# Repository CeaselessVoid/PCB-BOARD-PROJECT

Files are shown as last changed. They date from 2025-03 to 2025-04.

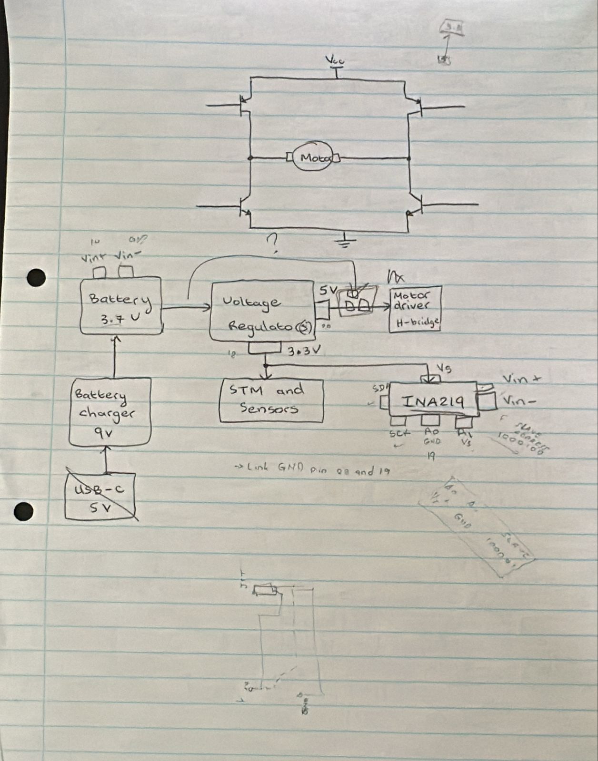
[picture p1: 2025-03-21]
Project_Roadmap.jpeg

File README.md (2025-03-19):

# PCB-BOARD-PROJECT
Currently we still need to flesh out our design in terms of component choice, back up designs and the actual design.
Below is all the data we have currently(the requirements of the project) :
1. Operate up to 4 motors bidirectionally with the pins available to you (listed in the power pinout table). You will need to control 2x brushed DC motors which could each draw 200mA at the highest voltage of a 1S1P battery (the battery is further specified in the battery section).The other 2x motors are for the auxiliary connection and need to operate 500mA each.
2. Place an INA219 for monitoring the battery on the I2C Bus and configure it correctly with respect to the hardware (cannot have BOTH A0 AND A1 on GND)
3. Charge the battery from the 9V input pin (listed in the power pinout table).
4. Have two charging modes for a higher and lower charging current for the battery (200mA, and approximately 600mA ±100mA from the battery perspective.
5. Integrate USB C and get 9V out of the USB Host
6. Provide 2x External Load Switching at 1A each (High Side connected to your 5V)
7. Provide a 3V3 5% accuracy (300mA max) and 5V Out 5% accuracy (1.5A max)
8. Provide an ON/OFF switch. OFF state: battery draw <30uA. ON state: can provide your robot peak current of 2A. The switch needs to shut down 5V and 3V3.

So far we have locked in the components INA219 and possiblely the H-bridge. This will need to be deducted from our budget once we fin a suitable vendor.(As it stands we have $56.5 for the components).
Other points:
1. The board solution should be 82 x 60 (mm)
2. We cannot excede the budget
3. Deadline is the 28th of March (we should try to finalize well before this)
4. All components sourced from JLCPCB

Future things to add here: 
1. We need to add the schemetic and PCB design
2. Possible links to the datasheets we used for an easier time during report writing
3. Any computations we do(again mainly for reference)

https://cdn-shop.adafruit.com/datasheets/ina219.pdf - INA219

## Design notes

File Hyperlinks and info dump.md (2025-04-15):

This section just has links to datasheets and any other valuable info for the project. (Will try my best to keep it neat). It seems the hyperlinks to JLCPCB require a page refresh to show the data. 

1. INA219:
   
i) INA219AIDR:
 - https://jlcpcb.com/api/file/downloadByFileSystemAccessId/8559701789747400704 (Datasheet)
 - [https://jlcpcb.com/parts/componentSearch?searchTxt=INA219 ](https://jlcpcb.com/partdetail/TexasInstruments-INA219AIDR/C138706)(JLCPCB page)
   
ii) INA219AIDCNR: (Chosen)
- https://jlcpcb.com/api/file/downloadByFileSystemAccessId/8586200525100486656 (Linked datasheet but i have my doubts about it)
- [https://jlcpcb.com/parts/componentSearch?searchTxt=INA219](https://jlcpcb.com/partdetail/TexasInstruments-INA219AIDCNR/C87469) (JLCPCB page)
  
The other components in JLCPCB fell into two categories. Either to pricey to consider or too few component count. They ave been ignored.

2. Voltage Regulators:
   
2.1 DC-DC Converter - Boost.

i) HT7750B 
   - https://jlcpcb.com/partdetail/HoltekSemicon-HT7750B/C259932 (JLCPCB page)
   - https://www.alldatasheet.com/datasheet-pdf/view/142973/HOLTEK/HT7750.html (Datasheet)

ii) MT3540-F23 (Chosen)
   - https://jlcpcb.com/partdetail/xi_an_AerosemiTech-MT3540F23/C181783 (JLCPCB page)
   - https://jlcpcb.com/api/file/downloadByFileSystemAccessId/8586200699318751232 (Datasheet)

iii) TPS613222ADBVR
   - https://jlcpcb.com/partdetail/TexasInstruments-TPS613222ADBVR/C2071163 (JLCPCB page)
   - https://www.ti.com/cn/lit/ds/symlink/tps61322.pdf?ts=1742636762086&ref_url=https%253A%252F%252Fjlcpcb.com%252F (Datasheet)

2.2 LDO 

i) HT7533-1
   - https://jlcpcb.com/partdetail/HoltekSemicon-HT75331/C14289 (JLCPCB page)
   - https://jlcpcb.com/api/file/downloadByFileSystemAccessId/8579707787284303872 (Datasheet)
   
ii) AP2112K-3.3TRG1 (Chosen)
   - https://jlcpcb.com/partdetail/DiodesIncorporated-AP2112K_33TRG1/C51118 (JLCPCB page)
   - https://jlcpcb.com/api/file/downloadByFileSystemAccessId/8588881290191360000 (Datasheet)

iii) MIC5219-3.3YM5-TR
   - https://jlcpcb.com/partdetail/MicrochipTech-MIC5219_3_3YM5TR/C29613 (JLCPCB page)
   - https://jlcpcb.com/api/file/downloadByFileSystemAccessId/8586199085112037376 (Datasheet)

iv) TPAP2112K-3.3TRG1
   - https://jlcpcb.com/partdetail/TechPublic-TPAP2112K_33TRG1/C3021085 (JLCPCB page)
   - https://jlcpcb.com/api/file/downloadByFileSystemAccessId/8589835741104021504 (Datasheet)

2.3 Schottky Diodes

i) SS34
- https://jlcpcb.com/partdetail/mdd_microdiode_semiconductor-SS34/C8678 (JLCPCB page)
- https://jlcpcb.com/api/file/downloadByFileSystemAccessId/8586172667489079296 (Datasheet)

2.3 Inductor 

i) FTC252010S4R7MBCA (4.7uH)
   - https://jlcpcb.com/partdetail/6763480-FTC252010S4R7MBCA/C5832360 (JLCPCB page)
   - https://jlcpcb.com/api/file/downloadByFileSystemAccessId/8590904256692510720 (Datasheet)
   
3. Battery Chargers

3.1 TP4056-42-ESOP8
   - https://jlcpcb.com/partdetail/17264-TP4056_42ESOP8/C16581 (JLCPCB page)
   - https://jlcpcb.com/api/file/downloadByFileSystemAccessId/8588879072461508608 (Datasheet)

3.2 MP2617
   - https://jlcpcb.com/partdetail/Monolithic_PowerSystems-MP2617AGLZ/C3682812 (JCLPCB page)
   - https://jlcpcb.com/api/file/downloadByFileSystemAccessId/8590922724149837824 (Datasheet)

3.3 TP5100
   - https://jlcpcb.com/partdetail/351706-TP5100/C379389 (JLCPCB page)
   - https://jlcpcb.com/api/file/downloadByFileSystemAccessId/8588884095233769472 (Datasheet)

3.4 BQ24074RGT (Chosen)
   - https://jlcpcb.com/partdetail/TexasInstruments-BQ24074RGTR/C54313 ( JLC Page)
   - https://www.ti.com/cn/lit/ds/symlink/bq24074.pdf?ts=1743070751216 (Datasheet)

3' Fast Charging Switch

i) FSW3157YSOT363G/TR
   - https://jlcpcb.com/parts/componentSearch?searchTxt=FSW3157YSOT363G%2FTR (JLC Page)
   - https://www.lcsc.com/datasheet/lcsc_datasheet_2407251614_Full-Way-FSW3157YSOT363G-TR_C32713320.pdf (Datasheet)

4. Motor Driver

i) DRV8838DSGR
   - https://jlcpcb.com/partdetail/TexasInstruments-DRV8838DSGR/C86667 (JLCPCB page)
   - https://www.ti.com/cn/lit/ds/symlink/drv8838.pdf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 (Datasheet)

ii) DRV8833PWPR (Chosen)
   - https://jlcpcb.com/partdetail/TexasInstruments-DRV8833PWPR/C50506 (JLCPCB page)
   - https://www.ti.com/cn/lit/ds/symlink/drv8833.pdf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 (Datasheet)
   - https://www.ti.com/lit/ds/symlink/drv8833.pdf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 (Option 2 Datasheet)

iii) GR6205-SOP-8
   - https://jlcpcb.com/partdetail/Gr-GR6205_SOP8/C18164411 (JLCPCB page)
   - https://jlcpcb.com/api/file/downloadByFileSystemAccessId/8553212736617000960 (Datasheet)
   
5. USB C connector
   
i) TYPE-C 6P(073) (Chosen)
   - https://jlcpcb.com/partdetail/ShouHan-TYPE_C_6P_073/C668623 (JLCPCB page)
   - https://jlcpcb.com/api/file/downloadByFileSystemAccessId/8588893482534100992 (Datasheet)

ii) TYPE-C 16P(073)
   - https://jlcpcb.com/partdetail/ShouHan-TYPE_C_16P_073/C668624 (JLCPCB page)
   - https://jlcpcb.com/api/file/downloadByFileSystemAccessId/8588905583437496320 (Datasheet)

iii) TYPE-C 16P QTWT
   - https://jlcpcb.com/partdetail/ShouHan-TYPE_C_16PQTWT/C5187472 (JLCPCB page)
   - https://jlcpcb.com/api/file/downloadByFileSystemAccessId/8589836178129661952 (Datasheet)
     
6. USB PD

i) CH224K
   - https://jlcpcb.com/partdetail/wch_jiangsu_Qin_heng-CH224K/C970725 (JLCPCB page)
   - https://jlcpcb.com/api/file/downloadByFileSystemAccessId/8588893165608296448 (Datasheet)

ii) HUSB237-AA001-DN06R (Chosen)
   - https://jlcpcb.com/partdetail/Hynetek-HUSB237_AA001DN06R/C22373734 (JLCPCB page)
   - https://jlcpcb.com/api/file/downloadByFileSystemAccessId/8590908931298979840 (Datasheet)

7. Load switching IC

i) TPS22908YZTR
   - https://jlcpcb.com/partdetail/TexasInstruments-TPS22908YZTR/C240334 (JLCPCB page)
   - https://www.ti.com/cn/lit/ds/symlink/tps22908.pdf?ts=1742892859966 (Datasheet)

ii) RT9742GGJ5
   - https://jlcpcb.com/partdetail/RichtekTech-RT9742GGJ5/C250547 (JLCPCB page)
   - https://jlcpcb.com/api/file/downloadByFileSystemAccessId/8588885201744879616 (Datasheet)

iii) AP2171WG-7  (Chosen)
   - https://jlcpcb.com/partdetail/DiodesIncorporated-AP2171WG7/C110466 (JLCPCB page)
   - https://jlcpcb.com/api/file/downloadByFileSystemAccessId/8588881297834328064 (Datasheet)

8. Passive components

8.1 Resistors

i) FRL1206JR430TS (430mΩ)
   - https://jlcpcb.com/partdetail/Fojan-FRL1206JR430TS/C2934307 (JLCPCB page)
   - https://jlcpcb.com/api/file/downloadByFileSystemAccessId/8590222769360441344 (Datasheet)

ii) 0603WAF1002T5E (10kΩ)
   - https://jlcpcb.com/partdetail/26547-0603WAF1002T5E/C25804 (JLCPCB page)
   - https://jlcpcb.com/api/file/downloadByFileSystemAccessId/8579706381320323072 (Datasheet)

iii) 0603WAF1501T5E (1.5kΩ)
   - https://jlcpcb.com/partdetail/23570-0603WAF1501T5E/C22843 (JLCPCB page)
   - https://jlcpcb.com/api/file/downloadByFileSystemAccessId/8579706144165986304 (Datasheet)

iv) 0603WAF9101T5E (9.1kΩ)
   - https://jlcpcb.com/partdetail/23987-0603WAF9101T5E/C23260 (JLCPCB page)
   - https://jlcpcb.com/api/file/downloadByFileSystemAccessId/8579706325305118720 (Datasheet)

v) 0603WAF3001T5E (3kΩ)
   - https://jlcpcb.com/partdetail/4618-0603WAF3001T5E/C4211 (JLCPCB page)
   - https://jlcpcb.com/api/file/downloadByFileSystemAccessId/8579706243143307264 (Datasheet)

vi) 1206W4J010JT5E (1Ω)
   - https://jlcpcb.com/partdetail/1761-1206W4J010JT5E/C1409 (JLCPCB page)
   - https://jlcpcb.com/api/file/downloadByFileSystemAccessId/8586177284142714880 (Datasheet)

vii) 0805W8F3000T5E (300Ω)
   - https://jlcpcb.com/partdetail/18305-0805W8F3000T5E/C17617 (JLCPCB page)
   - https://jlcpcb.com/api/file/downloadByFileSystemAccessId/8579706564124729344 (Datasheet)

viii) 0603WAF2201T5E (2.2kΩ)
   - https://jlcpcb.com/partdetail/4597-0603WAF2201T5E/C4190 (JLCPCB page)
   - https://jlcpcb.com/api/file/downloadByFileSystemAccessId/8579706158415659008 (Datasheet)

ix) 0603WAF3301T5E (3.3kΩ)
   - https://jlcpcb.com/partdetail/23705-0603WAF3301T5E/C22978 (JLCPCB page)
   - https://jlcpcb.com/api/file/downloadByFileSystemAccessId/8579706198066577408 (Datasheet)

x) 0805W8F1000T5E (100Ω)
   - https://jlcpcb.com/partdetail/18096-0805W8F1000T5E/C17408 (JLCPCB page)
   - https://jlcpcb.com/api/file/downloadByFileSystemAccessId/8562006687177089024 (Datasheet)
     
xi) FRL1206JR250TS (250mΩ)
   - https://jlcpcb.com/partdetail/Fojan-FRL1206JR250TS/C2934302 (JLCPCB page)
   - https://jlcpcb.com/api/file/downloadByFileSystemAccessId/8590222766902579200 (Datasheet)

xii) RL0603FR-070R15L (150mΩ)
   - https://jlcpcb.com/partdetail/Yageo-RL0603FR070R15L/C375502 (JLCPCB page)
   - https://jlcpcb.com/api/file/downloadByFileSystemAccessId/8588931929702354944 (Datasheet)

xiii) 0603WAF7502T5E (75kΩ)
   - https://jlcpcb.com/partdetail/23969-0603WAF7502T5E/C23242 (JLCPCB page)
   - https://jlcpcb.com/api/file/downloadByFileSystemAccessId/8579706316903792640 (Datasheet)

xiv) RLM12FTCMR020 (0.02Ω)
   - https://jlcpcb.com/partdetail/ta_iTech-RLM12FTCMR020/C393094 (JLCPCB page)
   - https://jlcpcb.com/api/file/downloadByFileSystemAccessId/8588933696833662976 (Datasheet)

8.2 Capacitors

i) CL05A225MQ5NSNC (2.2uF)
   - https://jlcpcb.com/partdetail/13164-CL05A225MQ5NSNC/C12530 (JLCPCB page)
   - https://jlcpcb.com/api/file/downloadByFileSystemAccessId/8586178550172540928 (Datasheet)
   
ii) CL21B103KBANNNC (10nF)
   - https://jlcpcb.com/partdetail/2062-CL21B103KBANNNC/C1710 (JLCPCB page)
   - https://jlcpcb.com/api/file/downloadByFileSystemAccessId/8579706770736144384 (Datasheet)

iii) CL10A105KB8NNNC (1uF)
   - https://jlcpcb.com/partdetail/16531-CL10A105KB8NNNC/C15849 (JLCPCB page)
   - https://jlcpcb.com/api/file/downloadByFileSystemAccessId/8556213788459761664 (Datasheet)

iv) CL10A106MQ8NNNC (10uF)
   - https://jlcpcb.com/partdetail/2043-CL10A106MQ8NNNC/C1691 (JLCPCB page)
   - https://jlcpcb.com/api/file/downloadByFileSystemAccessId/8586178152733552640 (Datasheet)

v) CL10A475KO8NNNC (4.7uF)
   - https://jlcpcb.com/partdetail/20375-CL10A475KO8NNNC/C19666 (JLCPCB page)
   - https://jlcpcb.com/api/file/downloadByFileSystemAccessId/8579707103462166528 (Datasheet)
 
vi) CL05B104KO5NNNC (100nF)
   - https://jlcpcb.com/partdetail/1877-CL05B104KO5NNNC/C1525 (JLCPCB page)
   - https://jlcpcb.com/api/file/downloadByFileSystemAccessId/8579707269996871680 (Datasheet)

vii) 01EC1809SHC10UF50V (10uF)
   - https://jlcpcb.com/partdetail/Knscha-01EC1809SHC10UF50V/C503219 (JLCPCB page)
   - https://jlcpcb.com/api/file/downloadByFileSystemAccessId/8588892766910341120 (Datasheet)

viii) ERR1HM121F16OT (120uF)
   - https://jlcpcb.com/partdetail/aishi_aihua_group-ERR1HM121F16OT/C106623 (JLCPCB page)
   - https://jlcpcb.com/api/file/downloadByFileSystemAccessId/8588898719165399040 (Datasheet)

9 Mechanical/rocker switches 

i) HX SK12F14G5 
   - https://jlcpcb.com/partdetail/Hanxia-HXSK12F14G5/C5149842 ( JLCPCB Page)
   - https://jlcpcb.com/api/file/downloadByFileSystemAccessId/8590009073539047424 (Datasheet)

ii) SS-12D11G3R
   - http://jlcpcb.com/partdetail/XkbConnection-SS12D11G3R/C843362 (JLCPCB page)
   - https://jlcpcb.com/api/file/downloadByFileSystemAccessId/8588889563317723136 (Datasheet)

iii) HX SS12D10G6 (Chosen)
   - https://jlcpcb.com/partdetail/Hanxia-HXSS12D10G6/C19189121 (JLCPCB page)
   - https://wmsc.lcsc.com/wmsc/upload/file/pdf/v2/lcsc/2311032126_hanxia-HX-SS12D10G6_C19189121.pdf (Datasheet)
   
10 Analogue Switches 

i) BL1551B
- https://jlcpcb.com/partdetail/bl_shanghai_belling-BL1551B/C2944066 (JLCPCB Page)
- https://jlcpcb.com/api/file/downloadByFileSystemAccessId/8589039779975061504 (Datasheet)

ii) ET3157
   - https://jlcpcb.com/partdetail/3170774-ET3157/C2904735 (JLCPCB page)
   - https://jlcpcb.com/api/file/downloadByFileSystemAccessId/8588944774351507456 (Datasheet)

iii) FSW3157YSOT363G/TR (Chosen)
   - https://jlcpcb.com/partdetail/fullway-FSW3157YSOT363GTR/C32713320 (JLCPCB page)
   - https://www.lcsc.com/datasheet/lcsc_datasheet_2407251614_Full-Way-FSW3157YSOT363G-TR_C32713320.pdf (Datasheet)

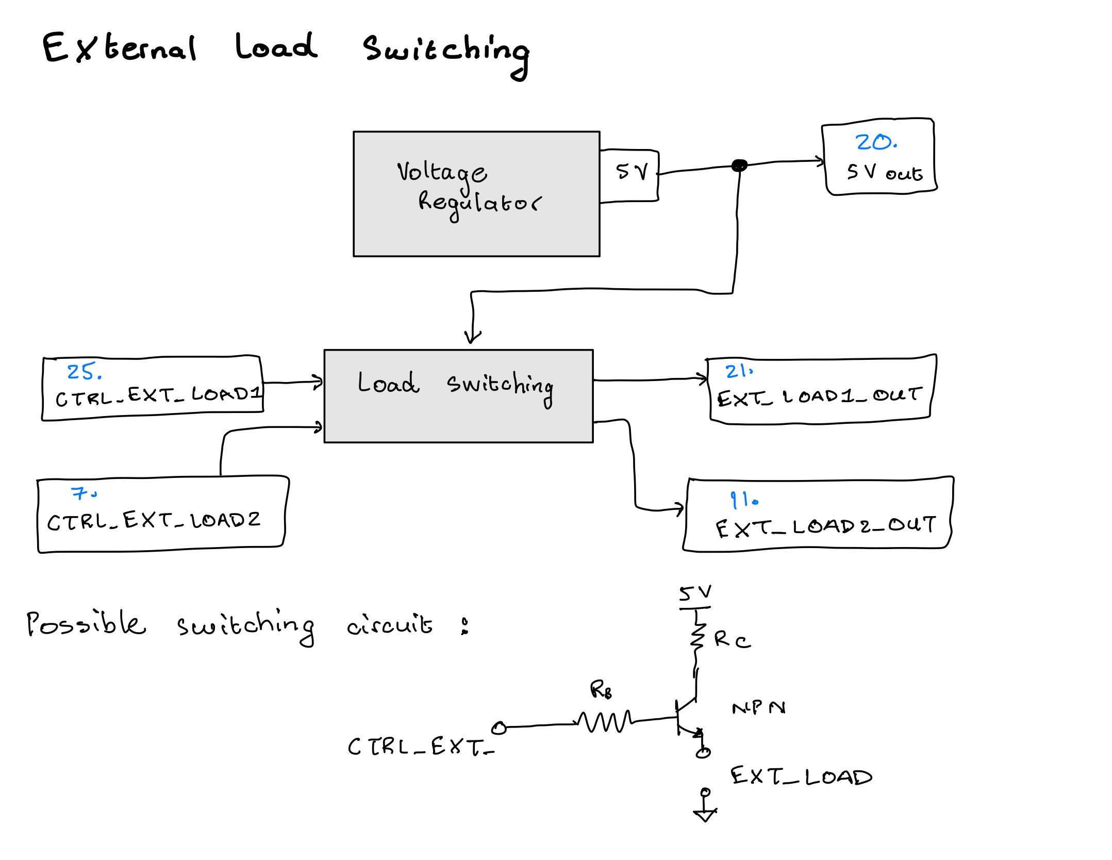
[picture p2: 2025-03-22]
Block Diagrams/External_Load_Switching.jpg

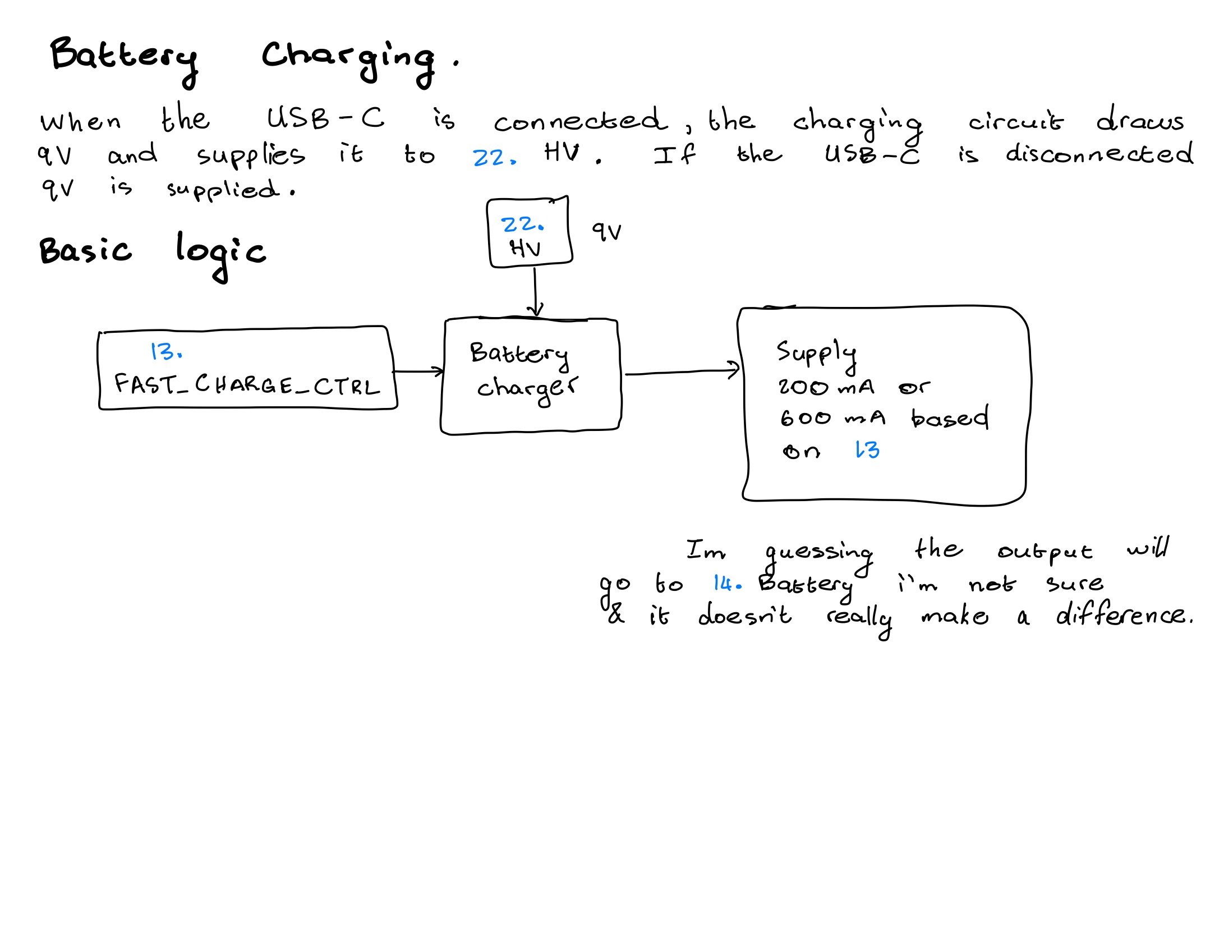
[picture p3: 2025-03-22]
Block Diagrams/Battery Charging.jpg

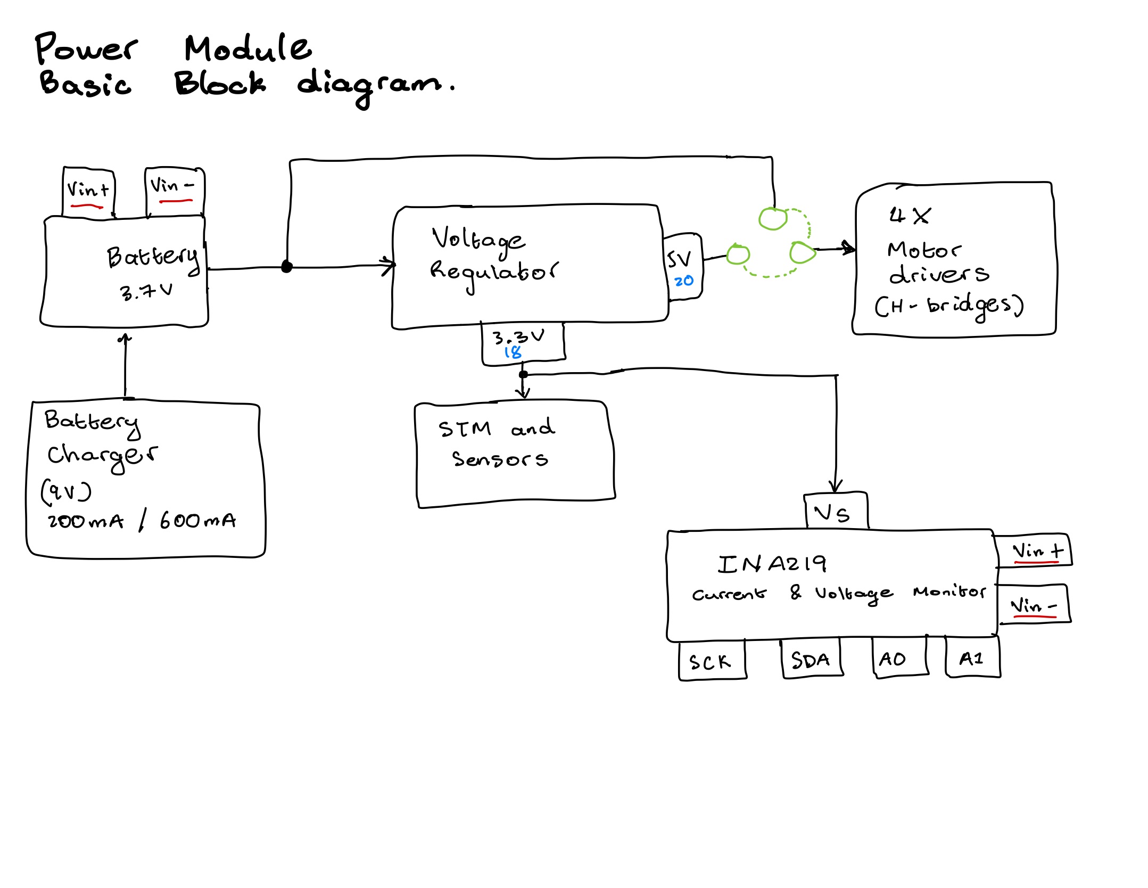
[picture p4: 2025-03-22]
Block Diagrams/PowerModule_BlockDiagram.jpg

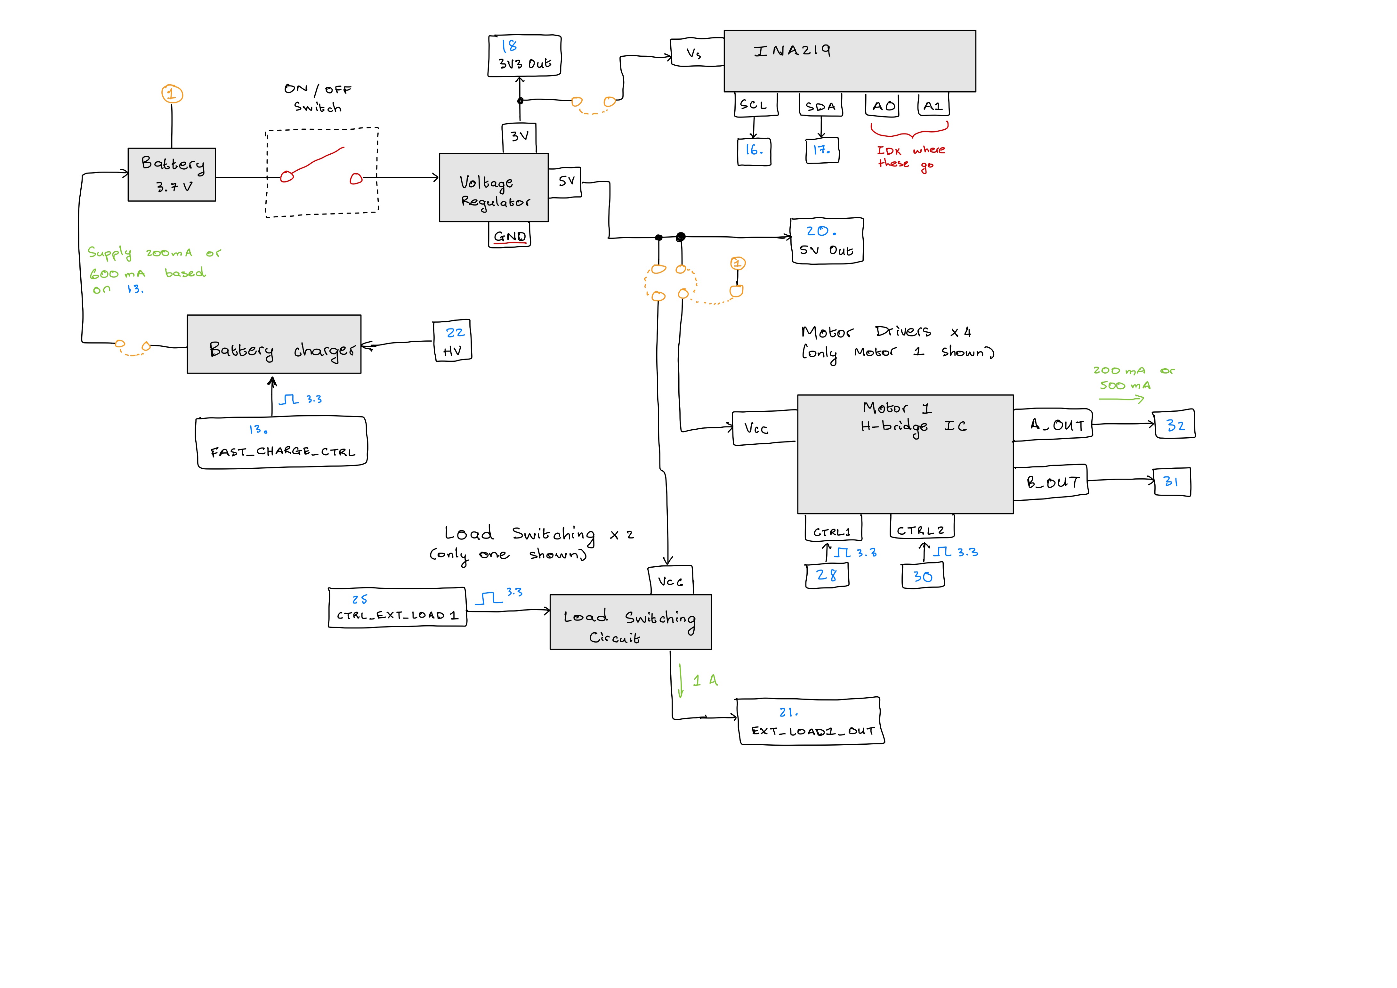
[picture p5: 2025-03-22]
Block Diagrams/Overall flow Diagram.jpg

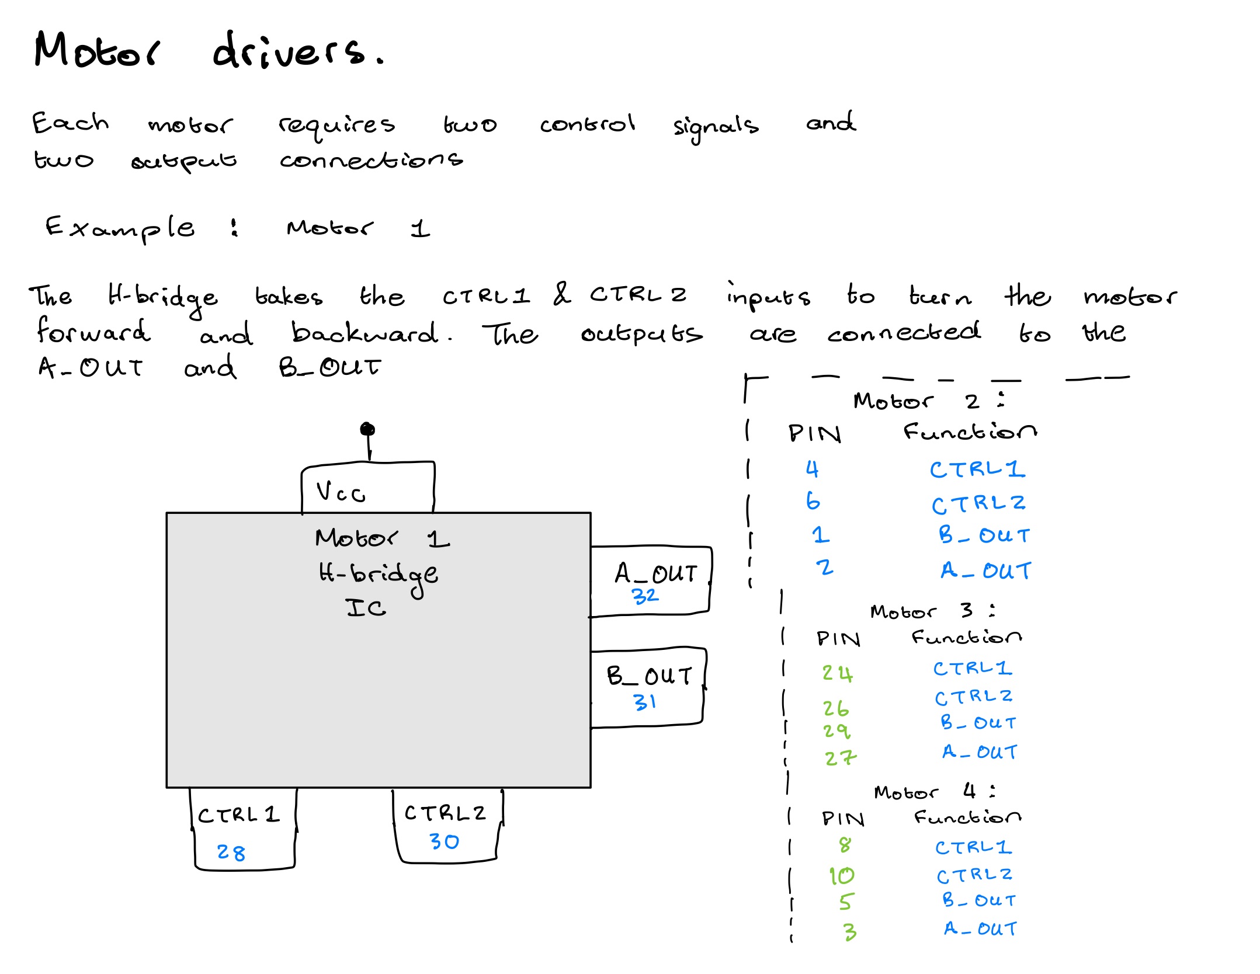
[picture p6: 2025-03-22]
Block Diagrams/Motor_Drivers.jpg

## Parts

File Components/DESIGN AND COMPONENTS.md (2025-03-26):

This section details our design choices (making reference to our roadmap). Discussed is the component lists and the choice behind the selection.Add to it how you see fit.

1. INA219.
   
This is one of the compulsory components. According to JLCPCB we have a choice between INA219AIDCNR and INA219AIDR. This was after eliminating the more expensive or rare components. This component is **extended** hence will incure an added cost to use. From my analysis i would choice the INA219AIDCNR since it is cheaper and its datasheet implies that it has the same functionality as its counterpart. Additionally, the component is smaller compared to INA219AIDR hence helps with abiding to the space constraints.

Conclusion, we can go with INA219AIDCNR (datasheet linked) which is 0.6$ (net charge of 1.2$ for the board).

2. Voltage Regulator.
   
2.1 DC to DC convertor (Boost type)

This voltage regulator will work to provide a 5V output from the 3.7V battery supply. Our choices are HT7750B, MT3540-F23 and TPS613222ADBVR. None of these were basic but in terms of cost MT3540-F23 is the cheapest. To set up the voltage regulator all three need additional components (inductors, resistors, diodes or capacitors). HT7750B achieves this while only needing three bonus components but only has a fixed 5V output. MT3540-F23 requires the most extra components but the output voltage can be configured by changing the resistor values. In terms of flexibility MT3540-F23 is a good component but it will take up more space. TPS613222ADBVR is a balanced piece(it's fixed to 5v output and the cost lies between the other two). Given that the budget takes priority we might want to consider the MT3540-F23. Another bonus is it has the 1.5A output current we desire.

2.2 LDO 

This voltage regulator will work to provide 3.3V output from the 3.7V battery supply. Our choices are AP2112K-3.3TRG1, MIC5219-3.3YM5-TR, HT7533-1(extended variant),HT7533-1(basic variant) and TPAP2112K-3.3TRG1 (all other components are extended). In terms of cost AP2112K-3.3TRG1 and HT7533-1(extended variant) are the cheeapest. To set up the voltage regulator capacitors are required. The main features to consider is the dropout voltage and the supply voltage. Using this we can eliminate HT7533-1(extended variant) and HT7533-1(basic variant) since the requirement for regulation is Vin = Vout + 2V. The choice between TPAP2112K-3.3TRG1, AP2112K-3.3TRG1 and MIC5219-3.3YM5-TR is tricky since MIC5219-3.3YM5-TR has a better PSRR but is more expensive with a higher dropout voltage. AP2112K-3.3TRG1 is the cheapest of the bunch but has a lower PSRR. For cost reasons we can eliminate MIC5219-3.3YM5-TR and the TPAP2112K-3.3TRG1. The AP2112K-3.3TRG1 was choosen since it was the most cost appropriate however the TPAP2112K-3.3TRG1 could work better since it has the highest PSRR while also being cheaper than MIC5219-3.3YM5-TR.

3. Bidirectional motor control

This will be done using H-bridge IC (s). Our choices are DRV8833PWPR, GR6205-SOP-8, and DRV8838DSGR. In terms of cost the GR6205-SOP-8 is the cheapest but it also has the the lowest output current rating at 200 mA. This means it can run the 200 mA motors but will fail for the higher current demand motors. Focusing on current rating the DRV8838DSGR is out best bet since it has a current rating of 1.8 A hence should run both motors and any other high current motors that might be brought in the future. Unfortunately, it can only drive one motor at a time hence 4 IC(s) are required which affects both cost and space. Our best an only option is the 
DRV8833PWPR which drives two motors with a current rating of 1.5 A.

4. USB PD

This will form part of the power negotiation circuit and will work with the USB-C connection to get 9v from host. Our choices are CH224K and the HUSB237-AA001-DN06R. In terms of price the HUSB237-AA001-DN06R is cheaper however the CH224K has more flexibility when it comes to configuration(does not need resistors). However, since we are only interested in basic power negotiation the cheaper option (HUSB237-AA001-DN06R) will work fine. Both have data communication functionality but it will not be utilized.

5. USB-C Connector

This will work in hand with the USB PD to negotiate for 9V from the Host. Our choices are TYPE-C 6P(073), TYPE-C 16P(073) and the TYPE-C 16P QTWT. The cheapest and simplest design was TYPE-C 6P(073). The other two seemed to offer dual connection which was not necessary for this project. Additionally, they took up more space. In conclusion, we pick the simpler solution (TYPE-C 6P(073)) since a more complex one is just redundant.

6. Load Switching IC

This will use the CRTL-EXT-load pins to provide and remove a 1A supply to a load.(we require 2 for the project). Our choices are TPS22908YZTR, RT9742GGJ5 and AP2171WG-7. In terms of price AP2171WG-7 is the cheapest. We need to consider the RDS(on) of each component since it controls the power dissipation of the IC. The TPS22908YZTR has the lowest RDS(on) however it only accepts a maximum of 3.6V. Since our board will give this section 5V we can eliminate it. Comparing the RT9742GGJ5 and AP2171WG-7 we note that the RT9742GGJ5 has a better RDS(on) but is more expensive. For this perticular design the load current is set to 1A hence the Power dissipated difference between RT9742GGJ5 and AP2171WG-7 is in the mW range hence we can settle for the cheaper component(AP2171WG-7 ). If the current requirement were to change the later would be a better choice despite its price.

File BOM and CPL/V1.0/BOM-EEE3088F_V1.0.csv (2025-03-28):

Comment | Designator | Footprint | LCSC | Quantity
AP2171W | U7,U8 | SOT-25-5_L3.0-W1.8-P0.95-LS3.0-BL | C110466 | 2
2.2uF | C25,C26 | C_0402 | C12530 | 2
1Ω | R13,R14 | R_1206 | C1409 | 2
100nF | C12,C13,C14,C20 | C_0402 | C1525 | 4
1uF | C1,C19,C2,C3,C5,C6 | C_0603 | C15849 | 6
10nF | C10,C9 | C_0805 | C1710 | 2
300Ω | R20 | R_0805 | C17617 | 1
MT3608 | U1 | SOT-23-5_L3.0-W1.7-P0.95-LS2.8-BR | C181783 | 1
HX SS12D10G6-WJ | U10 | SW-TH_3P-P4.80_HX-SS12D10G6-WJ | C19189121 | 1
4.7uF | C11,C15,C16,C4 | C_0603 | C19666 | 4
HUSB237-AA001-DN06R | U11 | TDFN-6_L2.0-W2.0-P0.65-TL-EP | C22373734 | 1
1.5kΩ | R16,R17,R19 | R_0603 | C22843 | 3
3.3kΩ | R1,R10,R2 | R_0603 | C22978 | 3
75kΩ | R22 | R_0603 | C23242 | 1
9.1kΩ | R9 | R_0603 | C23260 | 1
10kΩ | R12,R15,R23 | R_0603 | C25804 | 3
430m | R3,R4 | R1206 | C2934307 | 2
FSW3157YSOT363G/TR | U9 | SOT-363_L2.1-W1.3-P0.65-LS2.1-BL | C32713320 | 1
0.02 | R_SHUNT1 | R1206 | C393094 | 1
2.2kΩ | R6 | R_0603 | C4190 | 1
3kΩ | R18,R5 | R_0603 | C4211 | 2
10uF | C17,C18,C21,C22 | CAP-TH_BD5.0-P2.00-D0.8-FD | C503219 | 4
DRV8833PWP | U3,U5 | TSSOP-16_L5.0-W4.4-P0.65-LS6.4-BL-EP | C50506 | 2
AP2112K-3.3 | U4 | SOT-25-5_L2.9-W1.6-P0.95-LS2.8-BL | C51118 | 1
BQ24074RGT | U6 | QFN-16_L3.0-W3.0-P0.50-TL-EP1.7 | C54313 | 1
4.7uH | L1 | IND-SMD_L2.5-W2.0-VLS252012CX-150M | C5832360 | 1
TYPE-C 6P(073) | USB1 | TYPE-C-SMD_TYPE-C-6P_5 | C668623 | 1
SS34 | D1 | D_SMA | C8678 | 1
INA219AxD | U2 | SOT-23-8_L3.0-W1.7-P0.65-LS2.8-BR | C87469 | 1
Conn_01x02_Pin | J1 | JST_PH_B2B-PH-K_1x02_P2.00mm_Vertical |  | 1
Conn_02x16_Odd_Even | J2 | PinHeader_2x16_P2.54mm_Vertical |  | 1

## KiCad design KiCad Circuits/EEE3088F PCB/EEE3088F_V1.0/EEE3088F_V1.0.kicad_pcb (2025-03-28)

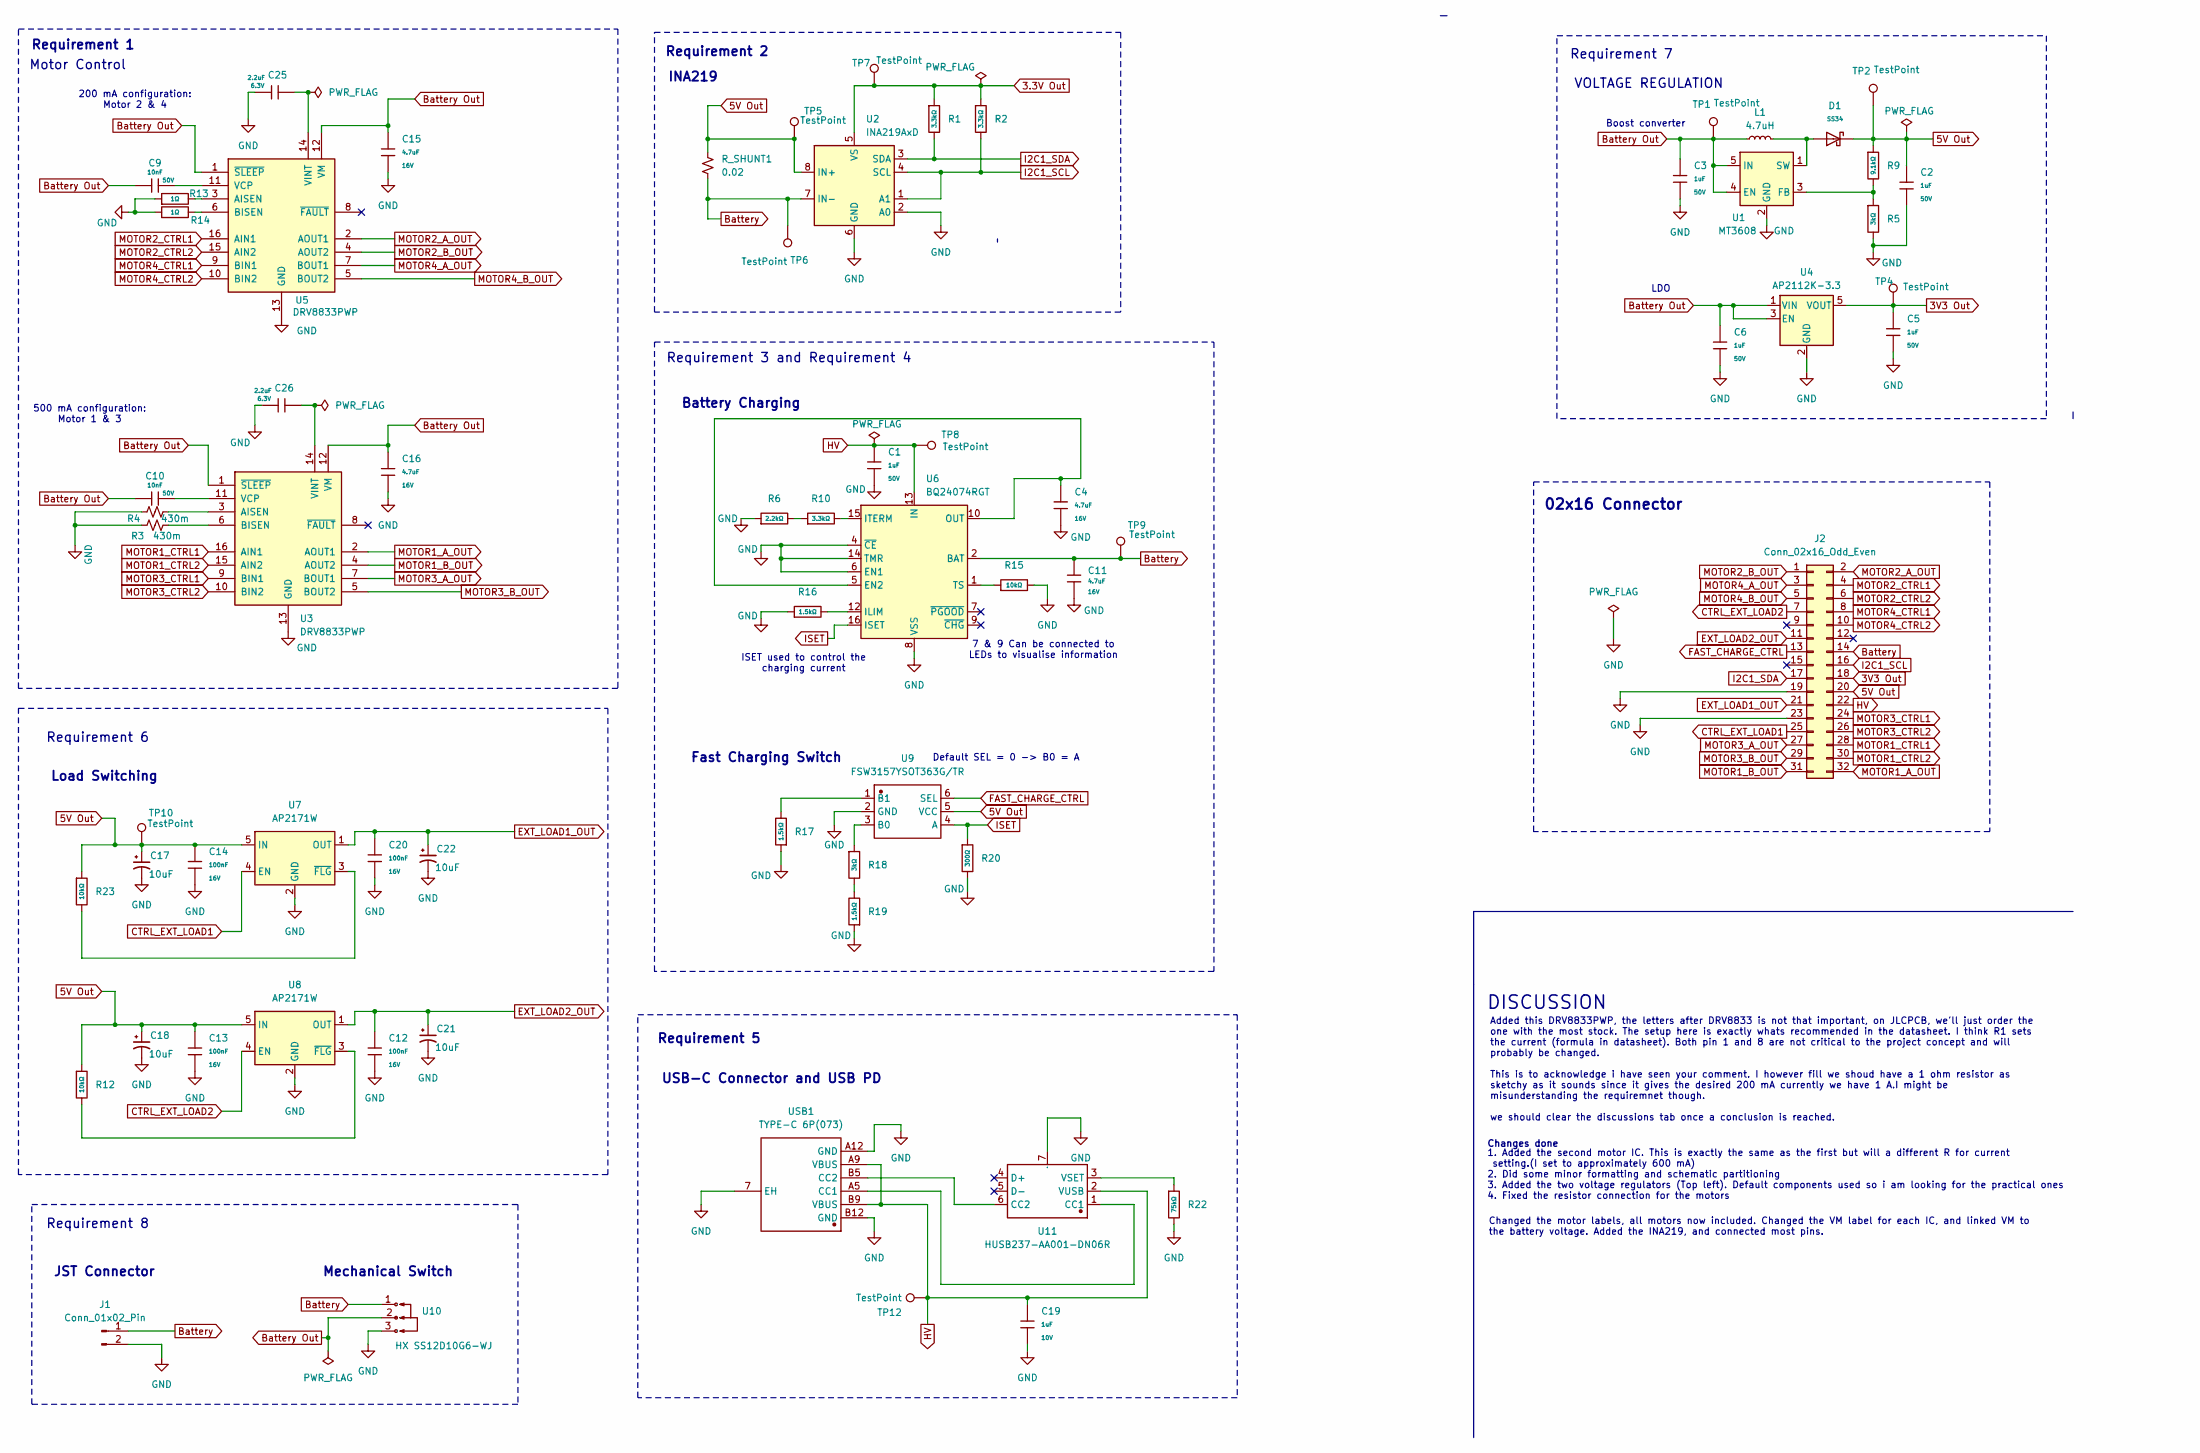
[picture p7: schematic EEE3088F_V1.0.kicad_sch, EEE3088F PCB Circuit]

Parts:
C1, C2, C3, C5, C6: 1uF; C_0603; Voltage Rated 50V; Tolerance ±10%; Part CL10A105KB8NNNC; LCSC C15849
C4, C11, C15, C16: 4.7uF; C_0603; Voltage Rated 16V; Tolerance ±10%; Part CL10A475KO8NNNC; LCSC C19666
C9, C10: 10nF; C_0805; Voltage Rated 50V; Tolerance ±10%; Part CL21B103KBANNNC; LCSC C1710
C12, C13, C14, C20: 100nF; C_0402; Voltage Rated 16V; Tolerance ±10%; Part CL05B104KO5NNNC; LCSC C1525
C17, C18, C21, C22: 10uF; CAP-TH_BD5.0-P2.00-D0.8-FD
C19: 1uF; C_0603; Voltage Rated 10V; Tolerance ±10%; Part CL10A105KB8NNNC; LCSC C15849
C25, C26: 2.2uF; C_0402; Voltage Rated 6.3V; Tolerance ±20%; Part CL05A225MQ5NSNC; LCSC C12530
D1: SS34; D_SMA; Forward Voltage (Vf@If) 550mV@3A; Reverse Voltage (Vr) 40V; Part SS34; LCSC C8678
J1: Conn_01x02_Pin; JST_PH_B2B-PH-K_1x02_P2.00mm_Vertical
J2: Conn_02x16_Odd_Even; PinHeader_2x16_P2.54mm_Vertical
L1: 4.7uH; IND-SMD_L2.5-W2.0-VLS252012CX-150M
R1, R2, R10: 3.3kΩ; R_0603; Overload Voltage (Max) 75V; Tolerance ±1%; Part 0603WAF3301T5E; LCSC C22978
R3, R4: 430m; R1206
R5, R18: 3kΩ; R_0603; Overload Voltage (Max) 75V; Tolerance ±1%; Part 0603WAF3001T5E; LCSC C4211
R6: 2.2kΩ; R_0603; Overload Voltage (Max) 75V; Tolerance ±1%; Part 0603WAF2201T5E; LCSC C4190
R9: 9.1kΩ; R_0603; Overload Voltage (Max) 75V; Tolerance ±1%; Part 0603WAF9101T5E; LCSC C23260
R12, R15, R23: 10kΩ; R_0603; Overload Voltage (Max) 75V; Tolerance ±1%; Part 0603WAF1002T5E; LCSC C25804
R13, R14: 1Ω; R_1206; Overload Voltage (Max) 200V; Tolerance ±1%; Part 1206W4F100KT5E; LCSC C17928
R16, R17, R19: 1.5kΩ; R_0603; Overload Voltage (Max) 75V; Tolerance ±1%; Part 0603WAF1501T5E; LCSC C22843
R20: 300Ω; R_0805; Overload Voltage (Max) 150V; Tolerance ±1%; Part 0805W8F3000T5E; LCSC C17617
R22: 75kΩ; R_0603; Overload Voltage (Max) 75V; Tolerance ±1%; Part 0603WAF7502T5E; LCSC C23242
R_SHUNT1: 0.02; R1206
TP1, TP2, TP4, TP5, TP6, TP7, TP8, TP9, TP10, TP12: TestPoint; TestPoint_Pad_4.0x4.0mm
U1: MT3608; SOT-23-5_L3.0-W1.7-P0.95-LS2.8-BR
U2: INA219AxD; SOT-23-8_L3.0-W1.7-P0.65-LS2.8-BR
U3, U5: DRV8833PWP; TSSOP-16_L5.0-W4.4-P0.65-LS6.4-BL-EP
U4: AP2112K-3.3; SOT-25-5_L2.9-W1.6-P0.95-LS2.8-BL
U6: BQ24074RGT; QFN-16_L3.0-W3.0-P0.50-TL-EP1.7
U7, U8: AP2171W; SOT-25-5_L3.0-W1.8-P0.95-LS3.0-BL
U9: FSW3157YSOT363G/TR; SOT-363_L2.1-W1.3-P0.65-LS2.1-BL; Manufacturer Part FSW3157YSOT363G/TR
U10: HX SS12D10G6-WJ; SW-TH_3P-P4.80_HX-SS12D10G6-WJ; Manufacturer Part HX SS12D10G6-WJ
U11: HUSB237-AA001-DN06R; TDFN-6_L2.0-W2.0-P0.65-TL-EP; Manufacturer Part HUSB237-AA001-DN06R
USB1: TYPE-C 6P(073); TYPE-C-SMD_TYPE-C-6P_5; Manufacturer Part TYPE-C 6P(073)

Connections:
3.3V Out: R1.1, R2.1, TP7.1, U2.5 (VS)
3V3 Out: C5.1, J2.18, TP4.1, U4.5 (VOUT)
5V Out: C2.1, C13.1, C14.1, C17.1, C18.1, D1.1, J2.20, R9.1, R12.1, R23.1, R_SHUNT1.1, TP2.1, TP5.1, TP10.1, U2.8 (IN+), U7.5 (IN), U8.5 (IN), U9.5 (VCC)
Battery: C11.1, J1.1, J2.14, R_SHUNT1.2, TP6.1, TP9.1, U2.7 (IN-), U6.2 (BAT), U6.3 (BAT), U10.1
Battery Out: C3.1, C6.1, C9.1, C10.1, C15.1, C16.1, L1.1, TP1.1, U1.4 (EN), U1.5 (IN), U3.1 (~SLEEP), U3.12 (VM), U4.1 (VIN), U4.3 (EN), U5.1 (~SLEEP), U5.12 (VM), U10.2
CTRL_EXT_LOAD1: J2.25, U7.4 (EN)
CTRL_EXT_LOAD2: J2.7, U8.4 (EN)
EXT_LOAD1_OUT: C20.1, C22.1, J2.21, U7.1 (OUT)
EXT_LOAD2_OUT: C12.1, C21.1, J2.11, U8.1 (OUT)
FAST_CHARGE_CTRL: J2.13, U9.6 (SEL)
GND: C1.2, C2.2, C3.2, C4.2, C5.2, C6.2, C11.2, C12.2, C13.2, C14.2, C15.2, C16.2, C17.2, C18.2, C19.2, C20.2, C21.2, C22.2, C25.1, C26.1, J1.2, J2.19, J2.23, R3.1, R4.1, R5.2, R6.1, R13.1, R14.1, R15.2, R16.1, R17.1, R19.1, R20.2, R22.2, U1.2 (GND), U2.2 (A0), U2.6 (GND), U3.13 (GND), U3.17 (GND), U4.2 (GND), U5.13 (GND), U5.17 (GND), U6.4 (~CE), U6.6 (EN1), U6.8 (VSS), U6.14 (TMR), U6.17 (VSS), U7.2 (GND), U8.2 (GND), U9.2 (GND), U10.3, U11.7 (GND), USB1.7 (EH), USB1.A12 (GND), USB1.B12 (GND)
HV: C1.1, C19.1, J2.22, TP8.1, TP12.1, U6.13 (IN), U11.2 (VUSB), USB1.A9 (VBUS), USB1.B9 (VBUS)
I2C1_SCL: J2.16, R2.2, U2.1 (A1), U2.4 (SCL)
I2C1_SDA: J2.17, R1.2, U2.3 (SDA)
ISET: R20.1, U6.16 (ISET), U9.4 (A)
MOTOR1_A_OUT: J2.32, U3.2 (AOUT1)
MOTOR1_B_OUT: J2.31, U3.4 (AOUT2)
MOTOR1_CTRL1: J2.28, U3.16 (AIN1)
MOTOR1_CTRL2: J2.30, U3.15 (AIN2)
MOTOR2_A_OUT: J2.2, U5.2 (AOUT1)
MOTOR2_B_OUT: J2.1, U5.4 (AOUT2)
MOTOR2_CTRL1: J2.4, U5.16 (AIN1)
MOTOR2_CTRL2: J2.6, U5.15 (AIN2)
MOTOR3_A_OUT: J2.27, U3.7 (BOUT1)
MOTOR3_B_OUT: J2.29, U3.5 (BOUT2)
MOTOR3_CTRL1: J2.24, U3.9 (BIN1)
MOTOR3_CTRL2: J2.26, U3.10 (BIN2)
MOTOR4_A_OUT: J2.3, U5.7 (BOUT1)
MOTOR4_B_OUT: J2.5, U5.5 (BOUT2)
MOTOR4_CTRL1: J2.8, U5.9 (BIN1)
MOTOR4_CTRL2: J2.10, U5.10 (BIN2)
unnamed: R6.2, R10.1
unnamed: R18.2, R19.2
unnamed: R5.1, R9.2, U1.3 (FB)
unnamed: D1.2, L1.2, U1.1 (SW)
unnamed: R4.2, U3.3 (AISEN)
unnamed: R3.2, U3.6 (BISEN)
unnamed: C10.2, U3.11 (VCP)
unnamed: C26.2, U3.14 (VINT)
unnamed: R13.2, U5.3 (AISEN)
unnamed: R14.2, U5.6 (BISEN)
unnamed: C9.2, U5.11 (VCP)
unnamed: C25.2, U5.14 (VINT)
unnamed: C4.1, U6.5 (EN2), U6.10 (OUT), U6.11 (OUT)
unnamed: R16.2, U6.12 (ILIM)
unnamed: R10.2, U6.15 (ITERM)
unnamed: R15.1, U6.1 (TS)
unnamed: R23.2, U7.3 (~FLG)
unnamed: R12.2, U8.3 (~FLG)
unnamed: R18.1, U9.3 (B0)
unnamed: R17.2, U9.1 (B1)
unnamed: U11.1 (CC1), USB1.A5 (CC1)
unnamed: U11.6 (CC2), USB1.B5 (CC2)
unnamed: R22.1, U11.3 (VSET)

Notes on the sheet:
Default SEL = 0 -> B0 = A
JST Connector
Battery Charging
Mechanical Switch
Requirement 5
INA219
ISET used to control the charging current
200 mA configuration: Motor 2 & 4
VOLTAGE REGULATION
Requirement 2
LDO
02x16 Connector
Added this DRV8833PWP, the letters after DRV8833 is not that important, on JLCPCB, we'll just order the one with the most stock. The setup here is exactly whats recommended in the datasheet. I think R1 sets the current (formula in datasheet). Both pin 1 and 8 are not critical to the project concept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
Requirement 1
USB-C Connector and USB PD
Requirement 3 and Requirement 4
Requirement 8
DISCUSSION
1. Added the second motor IC. This is exactly the same as the first but will a different R for current setting.(I set to approximately 600 mA) 2. Did some minor formatting and schematic partitioning 3. Added the two voltage regulators (Top left). Default components used so i am looking for the prac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
Changes done
Motor Control
Load Switching
500 mA configuration: Motor 1 & 3
Requirement 7
7 & 9 Can be connected to LEDs to visualise information
Fast Charging Switch
Changed the motor labels, all motors now included. Changed the VM label for each IC, and linked VM to the battery voltage. Added the INA219, and connected most pins.
Requirement 6
Boost converter

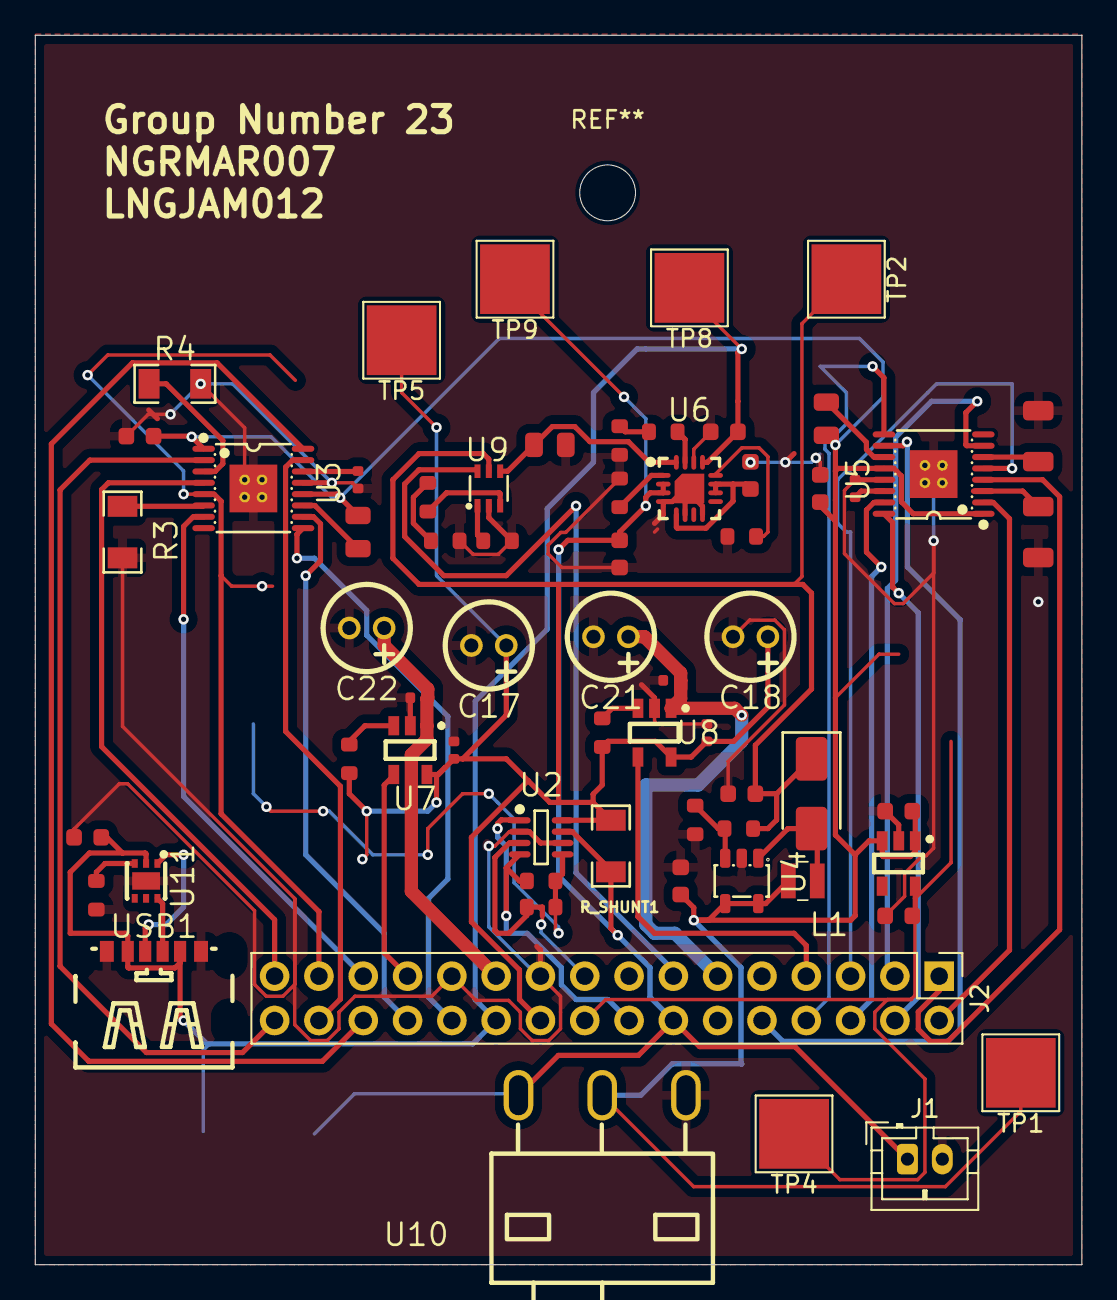
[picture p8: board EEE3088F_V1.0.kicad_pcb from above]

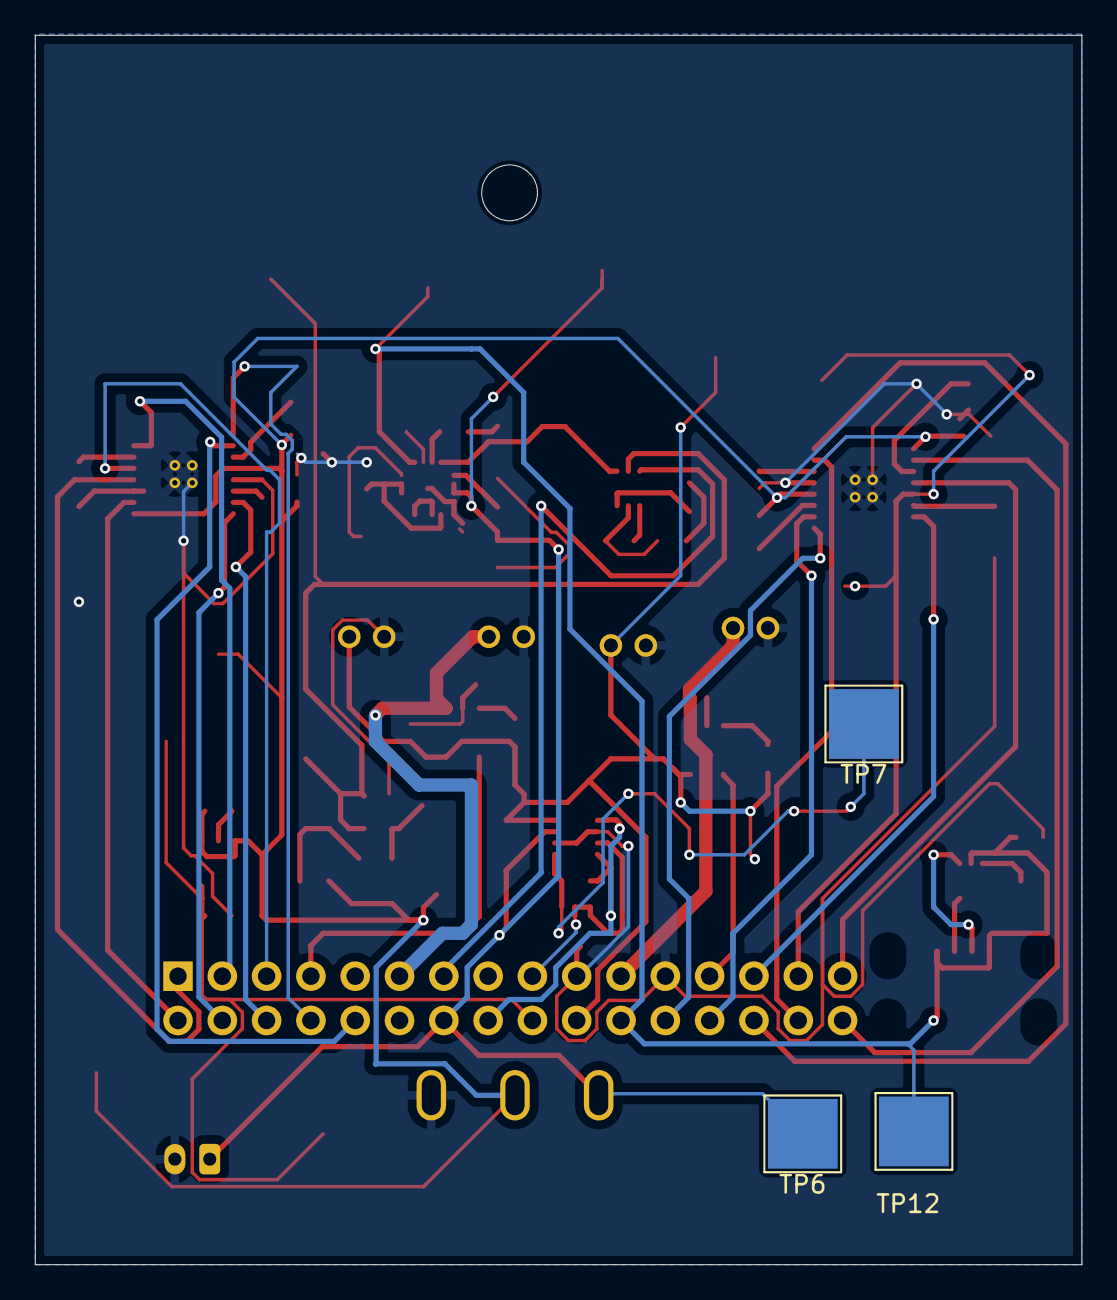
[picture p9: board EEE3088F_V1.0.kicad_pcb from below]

Board: 2 copper layers, 60.0 x 70.5 mm, 67 parts (3 on the bottom side), 54 nets.

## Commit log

2025-03-22 Block Diagrams for power module
    Helpful for understanding and pin outs
2025-03-22 Create Battery Charging.jpg
2025-03-22 Create Overall flow Diagram.jpg
2025-03-23 Added Kicad circuit (Blank so far)
    [EEE3088F_V1.0.kicad_pcb, EEE3088F_V1.0.kicad_sch]
2025-03-24 2x16 connector added
    [EEE3088F_V1.0.kicad_sch]
2025-03-24 Added 1 H-bridge (DRV8833PWP)
    [BOM-EEE3088F_V1.0.csv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]
2025-03-25 Added H-bridge and voltage regulators
    [EEE3088F_V1.0.kicad_sch]
2025-03-25 Added INA219 and did housekeeping
    [EEE3088F_V1.0.kicad_sch]
2025-03-26 Updated to v1.1
    [EEE3088F_V1.0.kicad_sch]
2025-03-26 Added Battery Charger
    [EEE3088F_V1.0.kicad_sch]
2025-03-26 Minor label added
    [EEE3088F_V1.0.kicad_sch]
2025-03-26 Added Load switching circuit and reorganised the page
    [EEE3088F_V1.0.kicad_sch]
2025-03-26 added INA219
    [EEE3088F_V1.0.kicad_sch]
2025-03-26 added footprints folder
    [EEE3088F_V1.0.kicad_sch]
2025-03-27 Analogue Switch added
    [EEE3088F_V1.0.kicad_sch]
2025-03-27 Added Mechanical Switch
    [EEE3088F_V1.0.kicad_sch]
2025-03-27 added symbols
    [EEE3088F_V1.0.kicad_sch]
2025-03-27 Increased page size and added footprint to imported components
    [EEE3088F_V1.0.kicad_sch]
2025-03-27 bigger page, added USB stuff
    [EEE3088F_V1.0.kicad_sch]
2025-03-27 Footprints added
    [EEE3088F_V1.0.kicad_sch]
2025-03-27 Done :)
    [EEE3088F_V1.0.kicad_sch]
2025-03-27 PCB added
    [EEE3088F_V1.0.kicad_pcb]
2025-03-27 Updated components, started PCB
    [EEE3088F_V1.0.kicad_pcb, EEE3088F_V1.0.kicad_sch]
2025-03-27 Pcb changes
    [EEE3088F_V1.0.kicad_pcb]
2025-03-27 Updated the Kicad pcb
    [EEE3088F_V1.0.kicad_pcb, EEE3088F_V1.0.kicad_sch]
2025-03-27 Component position complete
    [EEE3088F_V1.0.kicad_pcb]
2025-03-27 PCB connected but not error free
    [EEE3088F_V1.0.kicad_pcb]
2025-03-28 Edited Kicad
    [EEE3088F_V1.0.kicad_pcb, EEE3088F_V1.0.kicad_sch]
2025-03-28 Updated pcb (missing connections)
    [EEE3088F_V1.0.kicad_pcb]
2025-03-28 Changes in pcb
2025-03-28 Fixed pcb
    [EEE3088F_V1.0.kicad_pcb]
2025-03-28 Updated PCB
    [BOM-EEE3088F_V1.0.csv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]
2025-03-28 added test points
    [BOM-EEE3088F_V1.0.csv, EEE3088F_V1.0.kicad_pcb, EEE3088F_V1.0.kicad_sch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]
2025-03-28 Final PCB
    [EEE3088F_V1.0.kicad_pcb, EEE3088F_V1.0.kicad_sch]
